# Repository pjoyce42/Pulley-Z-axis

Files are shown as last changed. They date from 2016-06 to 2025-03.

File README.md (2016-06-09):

# Pulley-Z-axis
a metal core xy printer with pulleys for the z-axis

This is an open source, 3D printer with a sheet metal frame. The intent of this design is to provide a robust mechanical design that is easy for any machine shop to manufacture. Currently, the design does require use of a breakpress and laser cutter, but all the bends are sharp 90deg, and the parts could be modified to use off the shelf (or printed) corner brackets. All individual printed parts are relatively small, and there is minimal support required. I tried to reuse parts as much as possible to reduce the unique part count.

In addition to the sheet metal frame, I have designed a hotend mount with an integrated strain gauge. My hope is that the strain gauge can be used for experimentation to provide an objective measurement that can be used to troubleshoot errors, optimize print settings, and help gain better insight into the physics of the printing process. I also hope to use the strian gauge in the auto bed leveling process in place of an induction sensor, or limit switches. 

Here is a partial to-do list:

	• Bowden tube ingress location
	• Spool holder
	• Door
	• Carrying Handles
	• Power plug mount
	• e-stop switch
	• Webcam mount
		○ LED strip mount
	• Validate Bed design
	• Switches for vaious electronics parts
		○ Rpi
		○ Main power
		○ Relays
			§ Hot end fan
			§ PrintrBoard
			§ LEDs
			§ Heated bed
	• Design strain gauge logging interface
	• Write software to emulate z-switch based on strain gauge reading
	
	If you have any interest in helping, or questions about the design please reach out through github.

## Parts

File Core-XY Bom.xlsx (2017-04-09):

ITEM NO. | PART NUMBER | QTY .
30 | _608 | 1
52 | 30x30 fan | 3
62 | 8x3mm magnet | 4
61 | 9541K1 | 4
31 | BEARING INSERT | 1
44 | Bed bearing mount | 2
66 | Connector^Endstop_Op to_TCST2103 | 5
13 | core-XY bed | 1
22 | e3d .40mm nozzle | 1
21 | e3dv6 heater block | 1
20 | e3dv6 heatsink | 1
4 | Enclosure back | 1
3 | Enclosure front | 1
47 | Enclosure side panel | 2
5 | Enclosure top | 1
38 | end stop trigger | 1
48 | end stop trigger | 2
50 | end stop trigger | 2
33 | extruder arm | 1
29 | Extruder base | 1
25 | filament | 1
40 | filament spool holder | 1
42 | gantry holder | 2
49 | gantry holder-bushing | 2
39 | hatchbox filament spool | 1
12 | heated bed spacer | 1
24 | heater core | 1
32 | HOBBED PULLEY | 1
26 | hotend clamp and fan mount | 1
9 | hotend mount | 1
37 | hotend mount-bushing | 1
11 | Hotend strain gauge mount | 1
46 | lift notch | 2
67 | linear bearing | 6
43 | linear rod | 2
53 | linear rod | 4
10 | loadcell | 1
58 | M2X10 | 4
63 | M3x20 | 4
35 | M3x35 | 1
51 | M4 V-groove pulley | 20
41 | M4X25 | 16
8 | mk2b heated bed | 1
14 | motion nut | 1
65 | PCB^Endstop_Opto_TCS T2103 | 5
27 | print cooling nozzle | 1
28 | print cooling nozzle mirror | 1
15 | printrboard | 1
16 | printrboard mount | 1
17 | psu | 1
45 | PULLEY SPACER 1 | 2
59 | PULLEY SPACER 1 | 4
60 | PULLEY SPACER 1 | 4
68 | PULLEY SPACER 1 | 6
19 | raspberrypi_b_+_(assem bly) | 1
18 | rpi board mount | 1
36 | sheet metal gantry | 1
34 | SPRING | 1
23 | steel heat break | 1
54 | STEPPER | 4
64 | TCST2103^Endstop_Opto _TCST2103 | 5
6 | threaded rod | 1
55 | TUNING PEG | 4
57 | tuning peg mount | 4
56 | TUNING PEG RETAINER | 4
2 | XYbase | 1
1 | XY-frame | 1
7 | z-coupler | 1

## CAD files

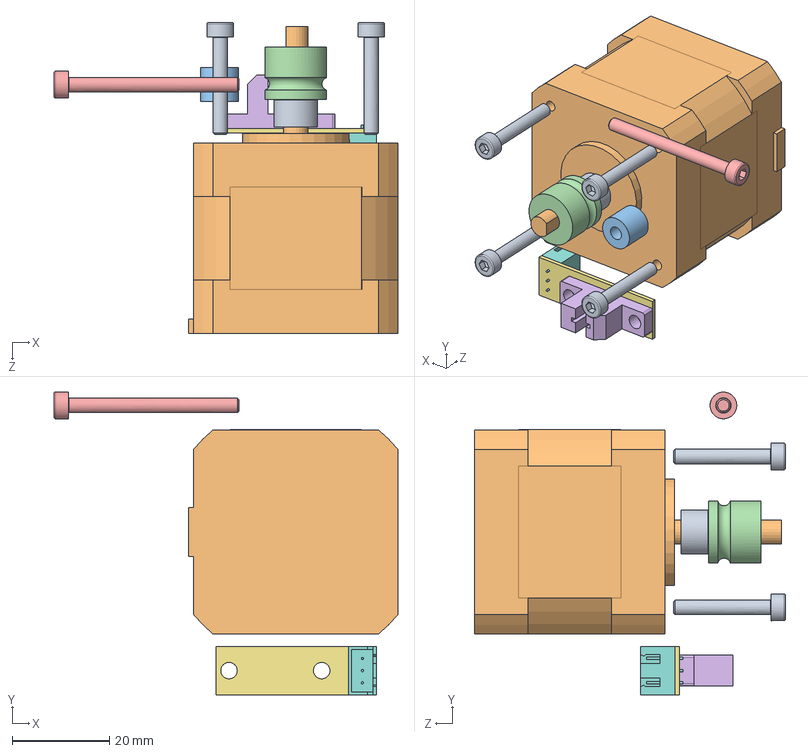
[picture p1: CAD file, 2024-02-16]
Extruder/Extruder.SLDASM
70.7 x 62.2 x 63.9 mm
M3x20 x 4
BEARING INSERT
M3x35
TCST2103^Endstop_Opto_TCST2103
PCB^Endstop_Opto_TCST2103
Connector^Endstop_Opto_TCST2103
MK8 HOBBED GEAR

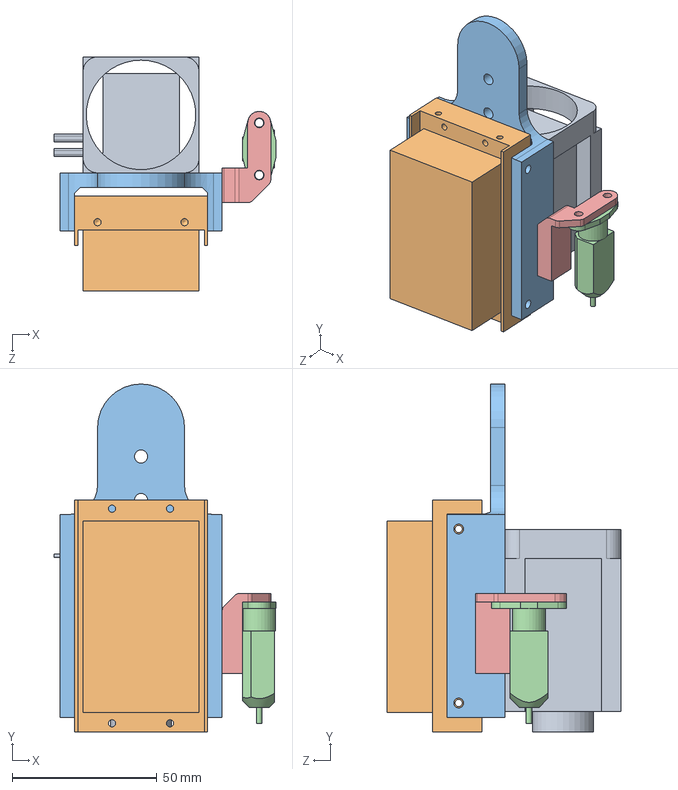
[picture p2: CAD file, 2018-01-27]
Laser/Laser Mount.SLDASM
76.5 x 120.0 x 80.8 mm
Laser Diode
Laser Driver
Laser Mount
BLTouch Smart
BLTouch mount

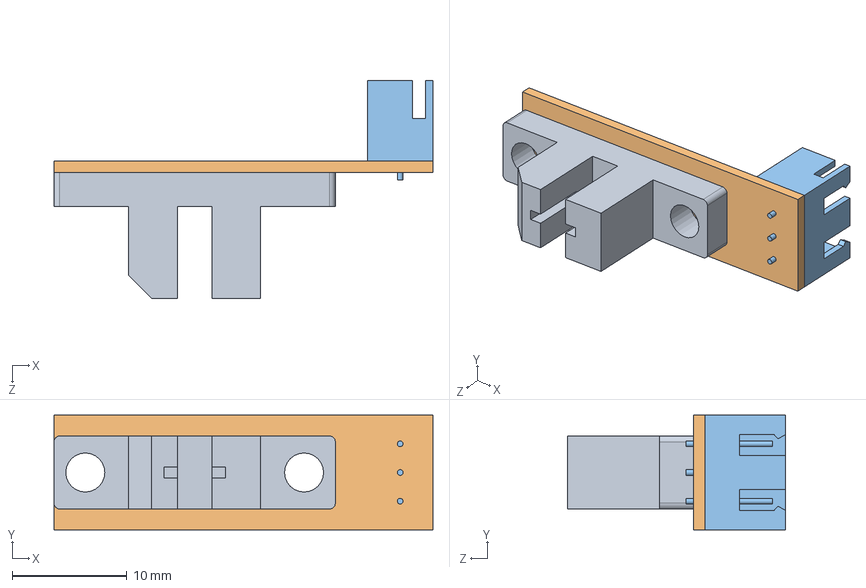
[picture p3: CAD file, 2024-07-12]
BortBot - Nov 2023/Endstop_Opto_TCST2103 - Nov 2023.SLDASM
33.0 x 10.0 x 19.0 mm
TCST2103^Endstop_Opto_TCST2103 - Nov 2023
PCB^Endstop_Opto_TCST2103 - Nov 2023
Connector^Endstop_Opto_TCST2103 - Nov 2023

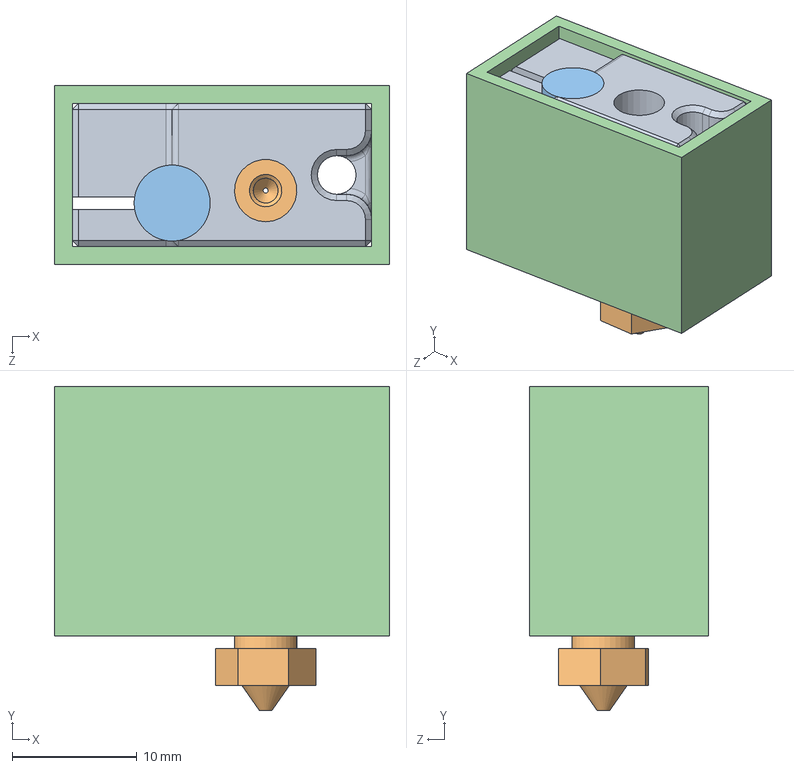
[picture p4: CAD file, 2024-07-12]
BortBot - Nov 2023/e3dv6 standin - Nov 2023.SLDASM
26.9 x 26.0 x 14.4 mm
E3d Volcano block - Nov 2023
e3d .40mm nozzle - Nov 2023
heater core - Nov 2023
Volcano Sock - Nov 2023

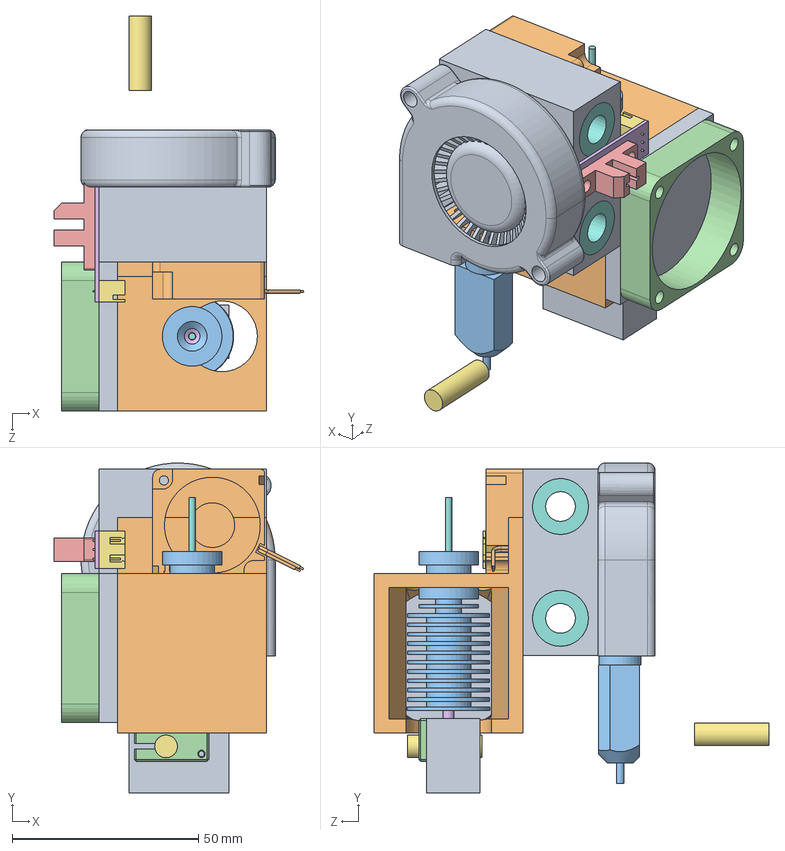
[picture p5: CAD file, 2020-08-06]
Modular Hot End/Modular Hot End.SLDASM
66.9 x 88.5 x 105.9 mm
Modular Hot End
Hot End Module
e3dv6 heatsink
e3dv6 heater block
e3d .40mm nozzle
steel heat break
heater core x 2
filament
BLTouch Angle Bracket
BLTouch Smart
40mmx40mm fan
TCST2103^Endstop_Opto_TCST2103
PCB^Endstop_Opto_TCST2103
Connector^Endstop_Opto_TCST2103
linear bearing x 2
Radial blower 30x10 v2

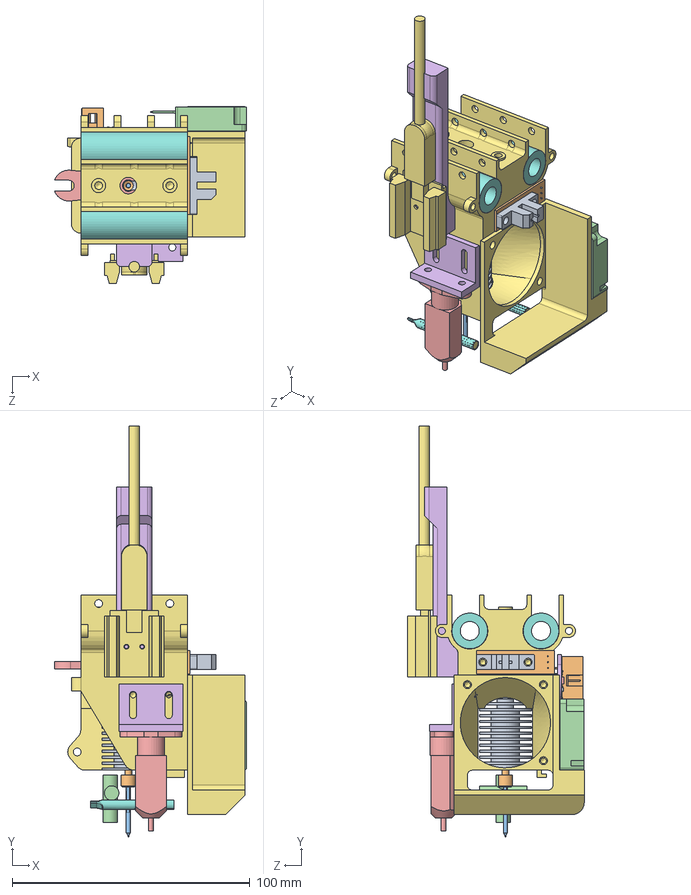
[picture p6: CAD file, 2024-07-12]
BortBot - Nov 2023/Bort Hot End Assy - Nov 2023.SLDASM
80.9 x 173.0 x 74.3 mm
e3dv6 heatsink - Nov 2023 x 2
steel heat break - Nov 2023 x 2
filament - Nov 2023 x 2
heater core - Nov 2023 x 2
BLTouch Smart - Nov 2023
BLTouch Angle Bracket - Nov 2023
Bort Hot End - Nov 2023
linear bearing - Nov 2023 x 2
TCST2103^Endstop_Opto_TCST2103 - Nov 2023
PCB^Endstop_Opto_TCST2103 - Nov 2023
Connector^Endstop_Opto_TCST2103 - Nov 2023
Radial blower 30x10 v2 - Nov 2023
collect clip - Nov 2023
Mini HDMI breakout board mount - Nov 2023
Micro HDMI Breakout board - Nov 2023
SOLID.step x 3
SOLID001.step
SOLID002.step
SOLID003.step x 6
SOLID005.step
SOLID010.step
Duet3_accelerometer PCB.step
Fan duct 3 + accel - Nov 2023
cooling tusk - Nov 2023 x 2

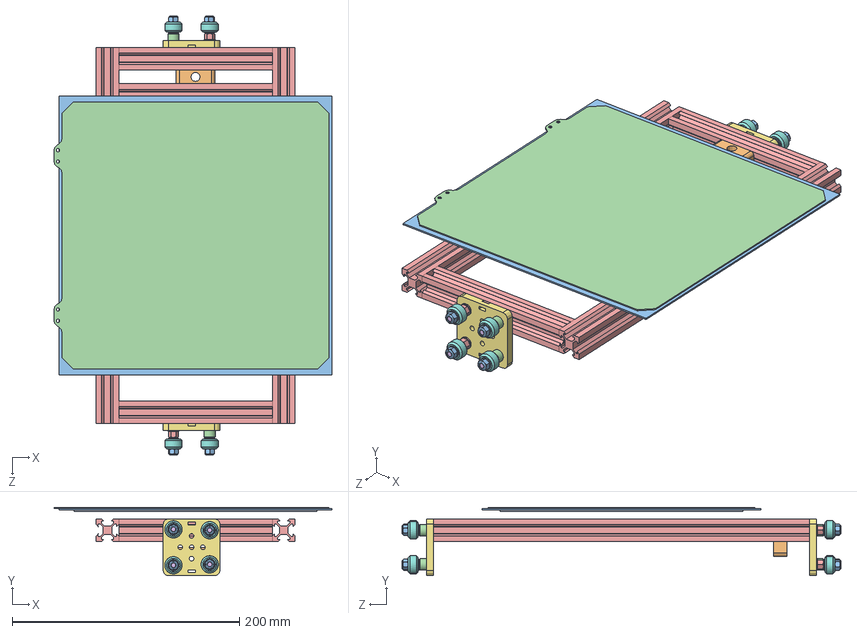
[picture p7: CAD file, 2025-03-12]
V-bed 3.SLDASM
244.5 x 60.2 x 385.8 mm
mk2b heated bed
8mm Acme Anti Backlash Nut Block
Heated Bed Platen
235 x 235 PEI build Plate
t-slot generic x 4
Low Profile Screw M5 x 8
Mini V Wheel Plate x 2
Delrin Mini V Wheel x 8
Ball Bearing 5 x 10 x 4.2 x 16
Precision Shim 8 x 5 x 1 x 16
Nylon Insert Lock Nut M5 x 8
Aluminum Spacer 6mm x 4
Mini Eccentric Spacer 6mm x 4

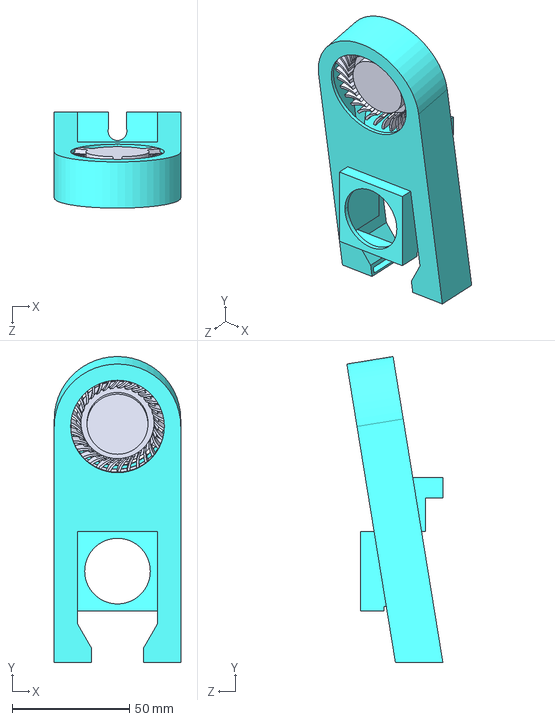
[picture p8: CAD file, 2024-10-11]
Simulations/Bort Hot End, Assy, Vertical Rails.STEP
54.0 x 130.6 x 41.1 mm
Blower fan 50mm
Fan shroud, Bortbot, vert

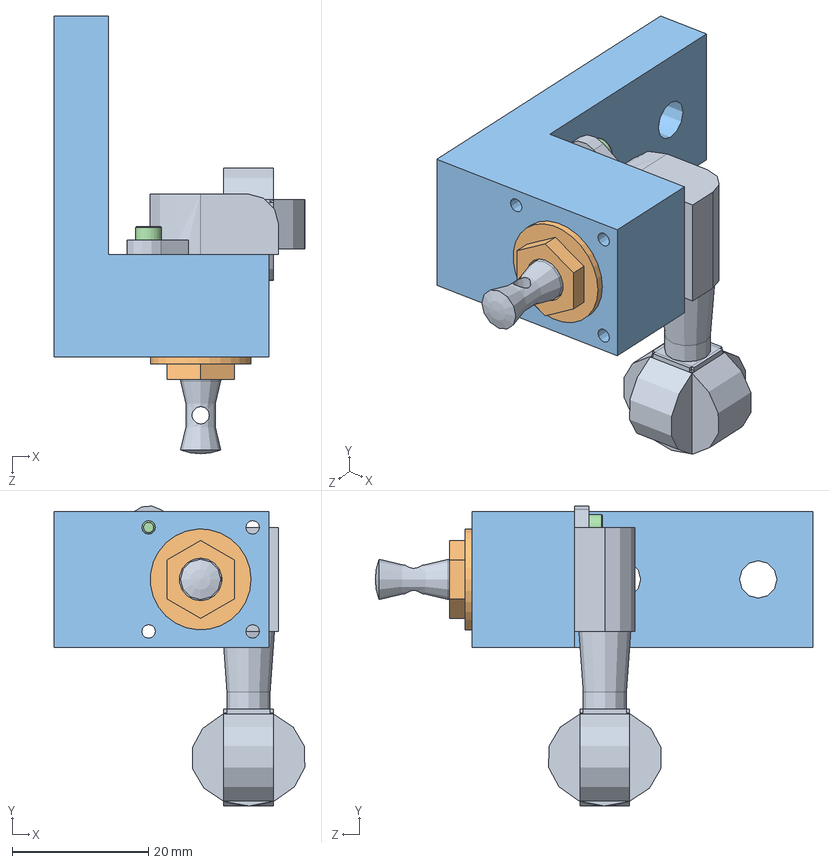
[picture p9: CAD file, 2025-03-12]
tuning peg tensioner 2.SLDASM
36.8 x 44.0 x 64.2 mm
TUNING PEG
TUNING PEG RETAINER
tuning peg mount 2
M2X10

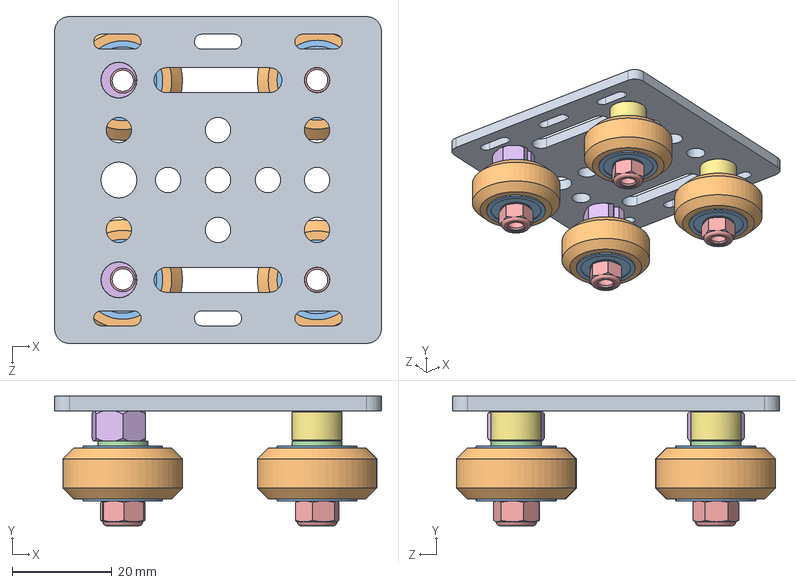
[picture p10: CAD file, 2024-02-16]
BortBot - Nov 2023/V-Slot Gantry Plate 1 - Nov 2023.SLDASM
65.5 x 26.0 x 65.5 mm
V-Slot Gantry Plate 20mm
Solid V Wheel x 4
Ball Bearing 5 x 16 x 5 x 8
Precision Shim 10 x 5 x 1 x 8
Nylon Insert Lock Nut M5 x 4
Eccentric Spacer 6mm x 2
Aluminum Spacer 6mm x 2

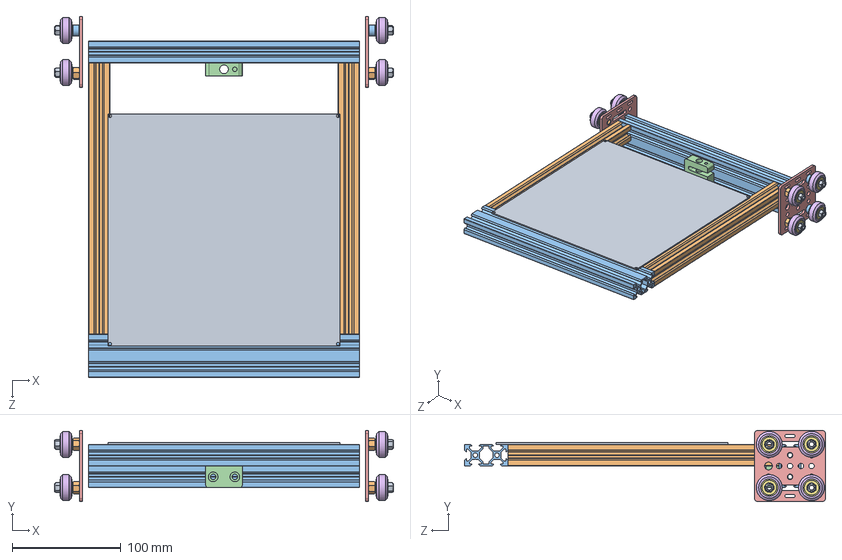
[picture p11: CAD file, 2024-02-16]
BortBot - Nov 2023/V-bed - Nov 2023.SLDASM
312.4 x 65.5 x 332.8 mm
mk2b heated bed
V-Slot 20x20x250 Linear Rail x 2
V-Slot 20x40x250 Linear Rail x 2
8mm Acme Anti Backlash Nut Block
V-Slot Gantry Plate 20mm x 2
Solid V Wheel x 8
Ball Bearing 5 x 16 x 5 x 16
Precision Shim 10 x 5 x 1 x 16
Nylon Insert Lock Nut M5 x 8
Eccentric Spacer 6mm x 4
Aluminum Spacer 6mm x 4

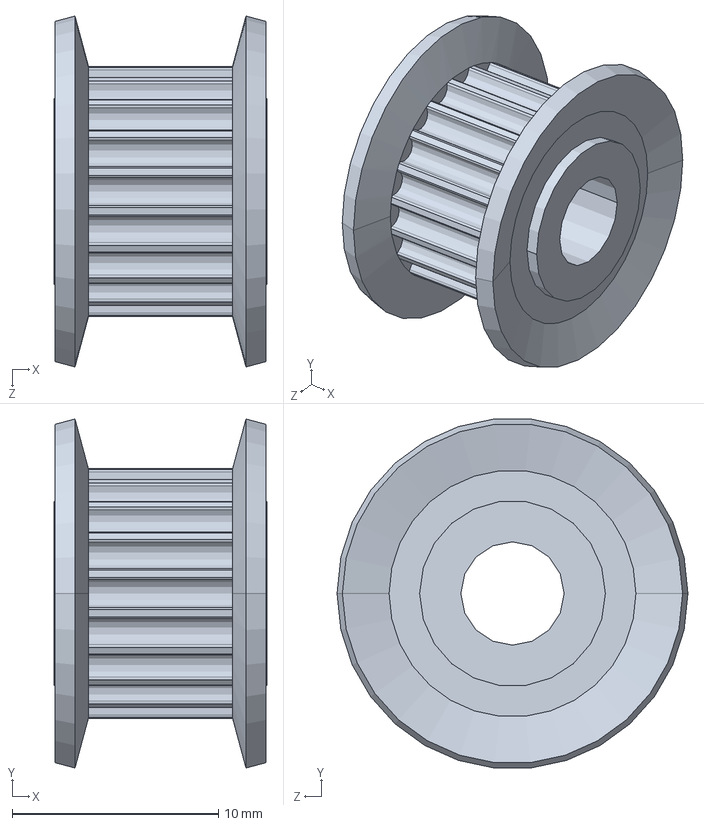
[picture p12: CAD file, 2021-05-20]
DWG Modular/GPA20GT2060_A_H5.sldasm
10.3 x 16.9 x 17.0 mm

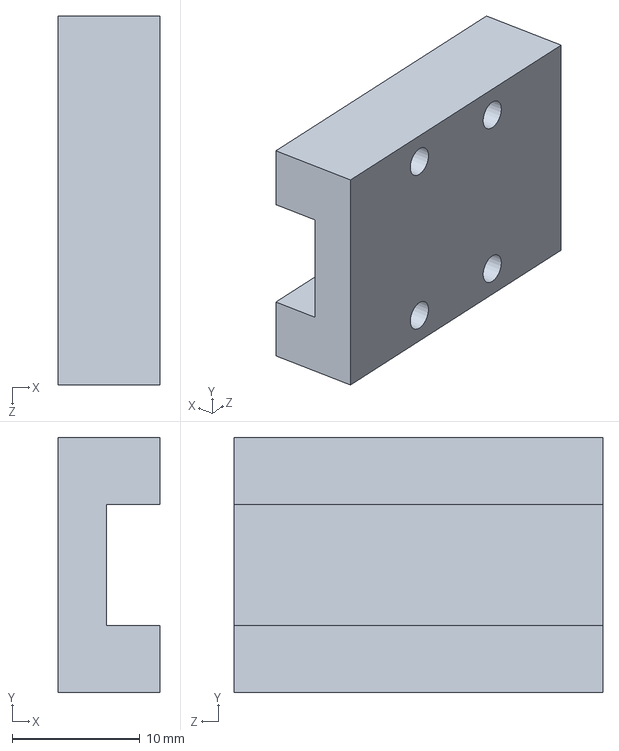
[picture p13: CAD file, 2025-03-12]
MGN9C Rail assy.SLDPRT
8.00 x 20.0 x 28.9 mm

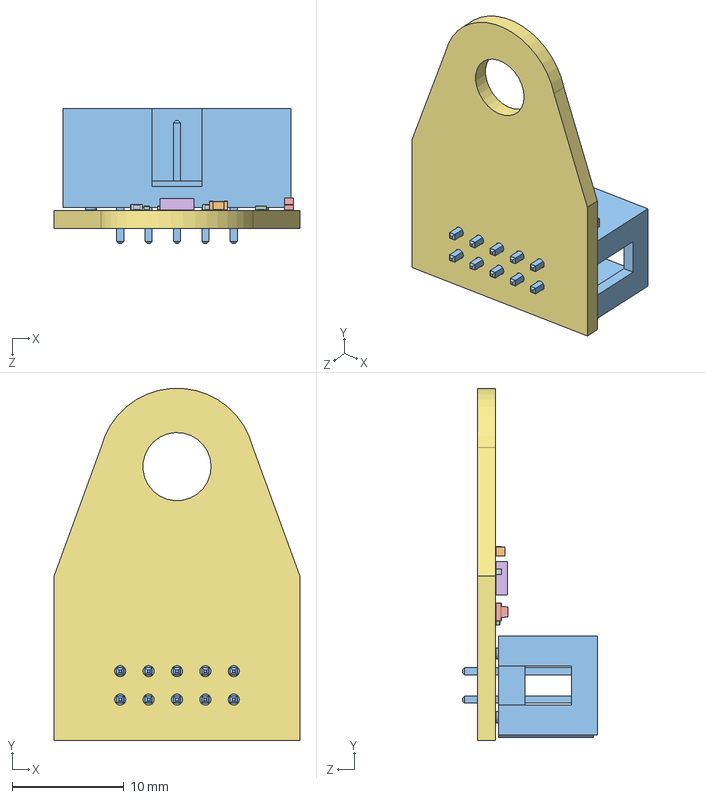
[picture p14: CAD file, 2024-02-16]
BortBot - Nov 2023/Duet3_accelerometer - Nov 2023.SLDASM
22.0 x 31.5 x 12.1 mm
SOLID.step x 3
SOLID001.step
SOLID002.step
SOLID003.step x 6
SOLID005.step
SOLID010.step
Duet3_accelerometer PCB.step

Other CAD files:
BortBot - Nov 2023/Solid V Wheel - Nov 2023.SLDASM
XY Gantry, Linear Rails, Assy.SLDASM
BortBot - Nov 2023/M4 PULLEY ASSEMBLY - Nov 2023.sldasm
Omron_Mag_Probe_Assembly.STEP.SLDASM
12 x 4 x 4 bearing.SLDPRT
235 x 235 PEI build Plate.SLDPRT
25x25x10 evercool fan.SLDPRT
2mm dowel.SLDPRT
30x30 fan.SLDPRT
3D_PCB4_2025-02-06 -2.SLDASM
3D_PCB4_2025-02-06.SLDASM
3D_PCB4_2025-02-06.step
40mm fan duct mirror.SLDPRT
40mmx40mm fan.SLDPRT
4mm dowel.SLDPRT
4mm linear bearing.SLDPRT
5010 fan mount.SLDPRT
604ZZ Bearing.SLDPRT
625vv.sldprt
6x3_Magnet.STEP.SLDPRT
9541K100_BUMPER WITH THREADED STUD.SLDPRT
A30 - Connector.SLDPRT
ASUS Blower fan.SLDPRT
BLTouch Spacer.SLDPRT
BLTouch sheet metal mount.SLDDRW
BLTouch sheet metal mount.SLDPRT
Bed Probe.SLDPRT
Bed bearing and nut.SLDASM
Bed bearing mount.SLDPRT
Belt1.SLDPRT
Blower fan 50mm.SLDPRT
Bort Hot End - 90deg rotate.SLDPRT
Bort Hot End - Mod.SLDPRT
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

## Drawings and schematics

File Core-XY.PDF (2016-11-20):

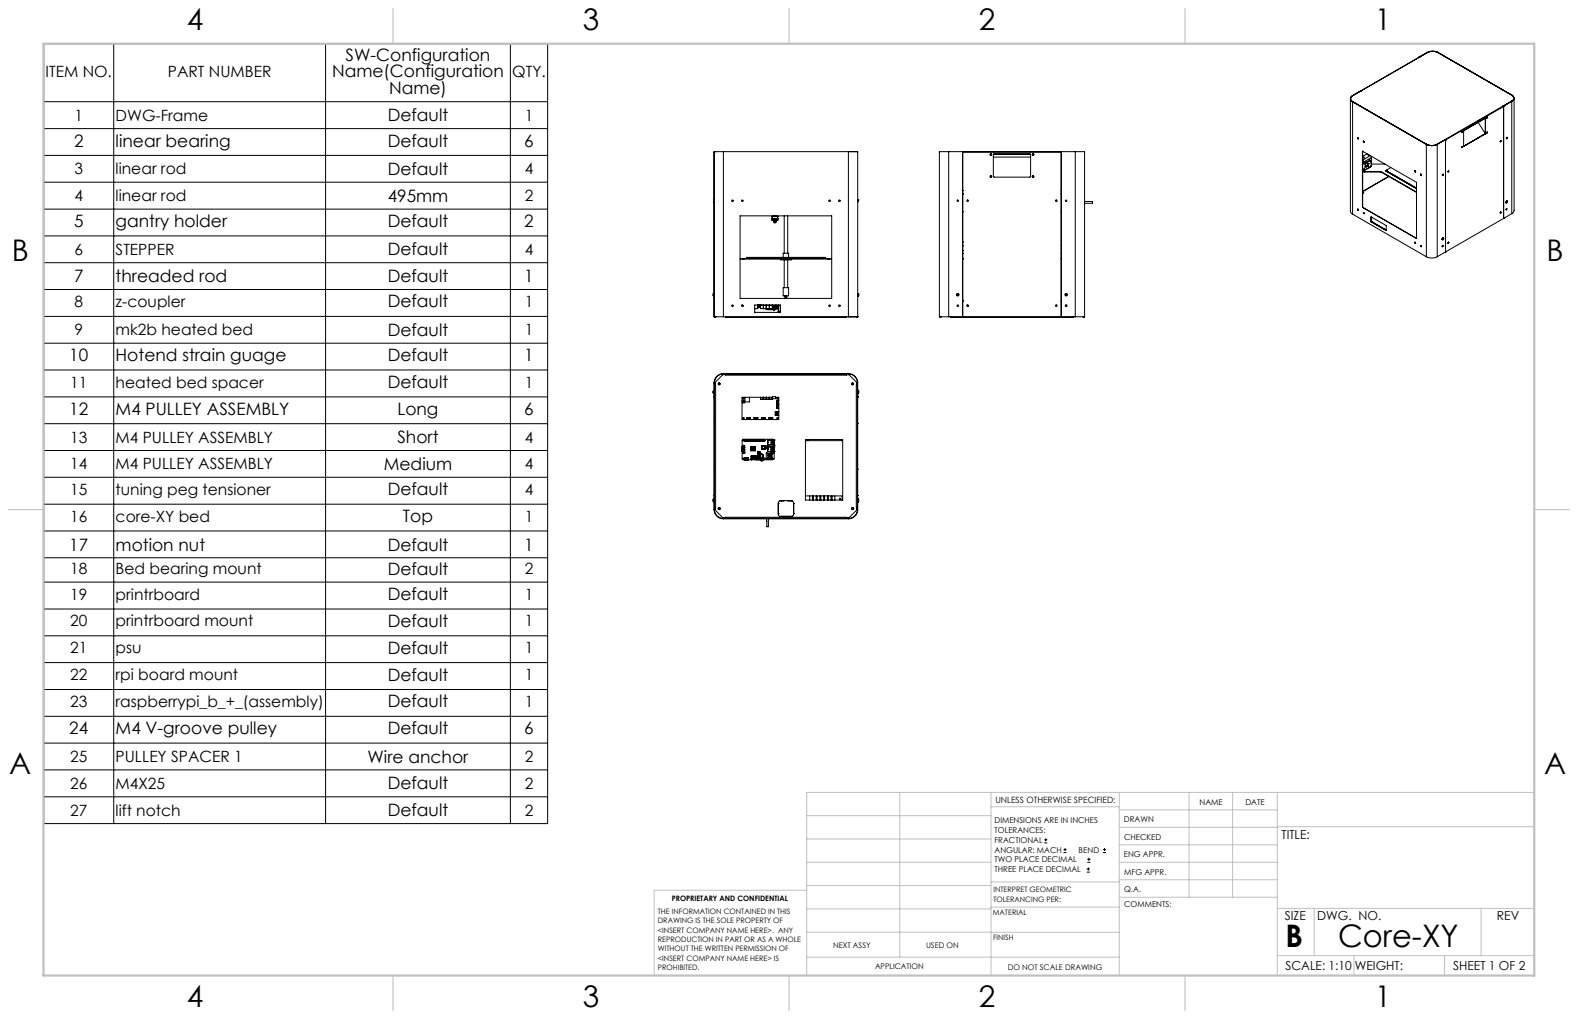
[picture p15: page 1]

ITEM NO. | PART NUMBER | SW-Configuration Name(Configuration Name) | QTY.

1 | DWG-Frame | Default | 1
2 | linear bearing | Default | 6
3 | linear rod | Default | 4
4 | linear rod | 495mm | 2
5 | gantry holder | Default | 2
6 | STEPPER | Default | 4
7 | threaded rod | Default | 1
8 | z-coupler | Default | 1
9 | mk2b heated bed | Default | 1
10 | Hotend strain guage | Default | 1
11 | heated bed spacer | Default | 1
12 | M4 PULLEY ASSEMBLY | Long | 6
13 | M4 PULLEY ASSEMBLY | Short | 4
14 | M4 PULLEY ASSEMBLY | Medium | 4
15 | tuning peg tensioner | Default | 4
16 | core-XY bed | Top | 1
17 | motion nut | Default | 1
18 | Bed bearing mount | Default | 2
19 | printrboard | Default | 1
20 | printrboard mount | Default | 1
21 | psu | Default | 1
22 | rpi board mount | Default | 1
23 | raspberrypi_b_+_(assembly) | Default | 1
24 | M4 V-groove pulley | Default | 6
25 | PULLEY SPACER 1 | Wire anchor | 2
26 | M4X25 | Default | 2
27 | lift notch | Default | 2

UNLESS OTHERWISE SPECIFIED: | | NAME | DATE
DIMENSIONS ARE IN INCHES TOLERANCES: FRACTIONAL ANGULAR: MACH BEND TWO PLACE DECIMAL THREE PLACE DECIMAL | DRAWN

CHECKED | | | TITLE:

ENG APPR.
MFG APPR.

INTERPRET GEOMETRIC TOLERANCING PER: | Q.A.
MATERIAL | | SIZE B | DWG. NO. Core-XY | REV

PROPRIETARY AND CONFIDENTIAL
THE INFORMATION CONTAINED IN THIS
DRAWING IS THE SOLE PROPERTY OF
<INSERT COMPANY NAME HERE>. ANY
REPRODUCTION IN PART OR AS A WHOLE
WITHOUT THE WRITTEN PERMISSION OF
<INSERT COMPANY NAME HERE> IS
PROHIBITED.

NEXT ASSY | USED ON | FINISH

APPLICATION | DO NOT SCALE DRAWING | | SCALE: 1:10 WEIGHT: | | SHEET 1 OF 2

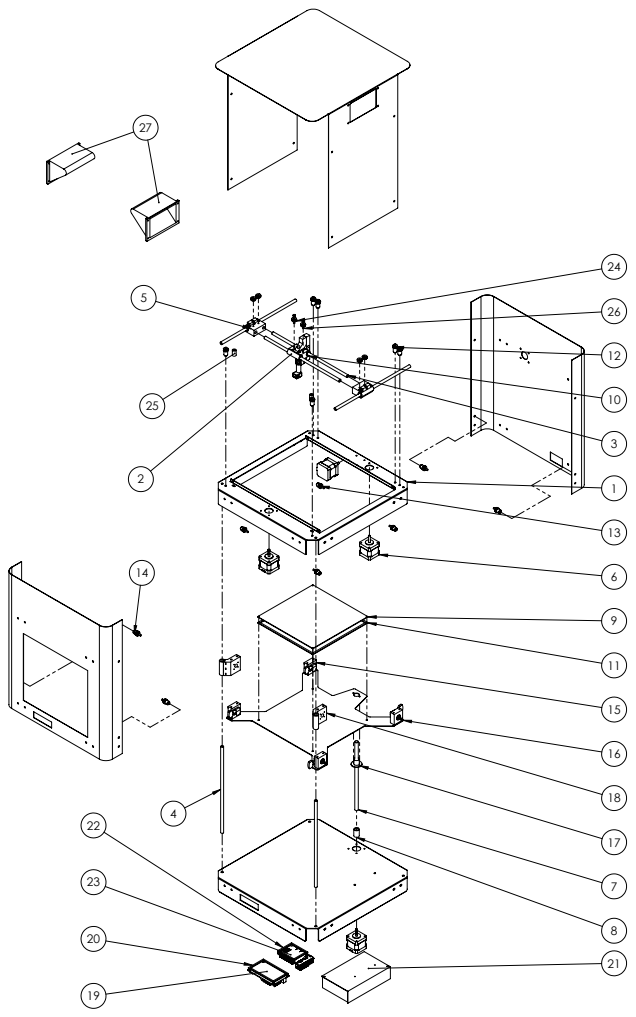
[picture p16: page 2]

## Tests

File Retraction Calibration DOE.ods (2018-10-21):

Run | X1 | X2 | X3 | X4 | X5 | X6 | X7 | Y1 | Y2
3 | -1 | 1 | -1 | -1 | 1 | -1 | 1 | 1 | 1
1 | -1 | -1 | -1 | 1 | 1 | 1 | -1 | 7 | 2
7 | -1 | 1 | 1 | -1 | -1 | 1 | -1 | 2 | 3
5 | -1 | -1 | 1 | 1 | -1 | -1 | 1 | 5 | 4
6 | 1 | -1 | 1 | -1 | 1 | -1 | -1 | 6 | 5
8 | 1 | 1 | 1 | 1 | 1 | 1 | 1 | 3 | 6
4 | 1 | 1 | -1 | 1 | -1 | -1 | -1 | 4 | 7
2 | 1 | -1 | -1 | -1 | -1 | 1 | 1 | 8 | 8
IDEAL | -1 | 1 | 0 | 0 | 1 | 0 | 0
 | Extra Restart Dist | Retract Dist | Layer Ht | Coast Dist | Wipe Dist | Retract During | Cooling Fan
1 | 0mm | 1.2mm | 0.15mm | 2mm | 2mm | Yes | 40.00%
2 | -1mm | 1.2mm | 0.15mm | 1.4mm | 1mm | Yes | 100.00%
3 | 0mm | 4mm | 0.15mm | 1.4mm | 2mm | No | 100.00%
4 | -1mm | 4mm | 0.15mm | 2mm | 1mm | No | 40.00%
5 | 0mm | 1.2mm | 0.4mm | 2mm | 1mm | No | 100.00%
6 | -1mm | 1.2mm | 0.4mm | 1.4mm | 2mm | No | 40.00%
7 | 0mm | 4mm | 0.4mm | 1.4mm | 1mm | Yes | 40.00%
8 | -1mm | 4mm | 0.4mm | 2mm | 2mm | Yes | 100.00%
IDEAL | 0mm | 4mm | 0.15mm | 1.4mm | 2mm | Yes | 40

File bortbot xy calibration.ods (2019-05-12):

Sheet: Sheet1
Trial run | X nominal | Y nominal | X1 real | Y1 Real | X2 real | Y2 Real | Xavg real | Yavg Real | X steps/mm | Y Steps/mm | X % error | Y % error
0 | 100 | 100 | 101.06 | 97.1 | 101.55 | 96.88 | 101.305 | 96.99 | 272.54 | 134.12 | 1.30500000000001 | -3.01000000000001
1 | 100 | 100 | 102.17 | 94.16 | 103.29 | 94 | 102.73 | 94.08 | 276.096647 | 130.082988 | 2.73 | -5.92
2 | 100 | 100 | 99.4 | 100.4 | 101.04 | 100.22 | 100.22 | 100.31 | 268.759512313832 | 138.268482142857 | 0.219999999999999 | 0.310000000000002
3 | 100 | 100 | 99.65 | 100.55 | 99.52 | 100.45 | 99.585 | 100.5 | 268.169539327312 | 137.841174501901 | -0.414999999999992 | 0.5
4 | 100 | 100 |  |  |  |  | #DIV/0! | #DIV/0! | 269.287080712268 | 137.15539751433 | #DIV/0! | #DIV/0!
5 | 100 | 100 |  |  |  |  | #DIV/0! | #DIV/0! | #DIV/0! | #DIV/0! | #DIV/0! | #DIV/0!
6 | 100 | 100 |  |  |  |  | #DIV/0! | #DIV/0! | #DIV/0! | #DIV/0! | #DIV/0! | #DIV/0!
7 | 100 | 100 |  |  |  |  | #DIV/0! | #DIV/0! | #DIV/0! | #DIV/0! | #DIV/0! | #DIV/0!
8 | 100 | 100 |  |  |  |  | #DIV/0! | #DIV/0! | #DIV/0! | #DIV/0! | #DIV/0! | #DIV/0!
9 | 100 | 100 |  |  |  |  | #DIV/0! | #DIV/0! | #DIV/0! | #DIV/0! | #DIV/0! | #DIV/0!
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

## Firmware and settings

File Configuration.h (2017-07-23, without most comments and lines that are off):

#define CONFIGURATION_H
#define CONFIGURATION_H_VERSION 010100
#define STRING_CONFIG_H_AUTHOR "(Patrick Joyce)" // Who made the changes.
#define SHOW_BOOTSCREEN
#define STRING_SPLASH_LINE1 SHORT_BUILD_VERSION // will be shown during bootup in line 1
#define STRING_SPLASH_LINE2 WEBSITE_URL         // will be shown during bootup in line 2
#define SERIAL_PORT 0
#define BAUDRATE 250000
  #define MOTHERBOARD BOARD_PRINTRBOARD
#define CUSTOM_MACHINE_NAME "BORT1"
#define EXTRUDERS 1
#define POWER_SUPPLY 0
#define TEMP_SENSOR_0 -1 //legacy from QU-BD Ups
#define TEMP_SENSOR_1 0
#define TEMP_SENSOR_2 0
#define TEMP_SENSOR_3 0
#define TEMP_SENSOR_4 0
#define TEMP_SENSOR_BED 0
#define DUMMY_THERMISTOR_998_VALUE 25
#define DUMMY_THERMISTOR_999_VALUE 100
#define MAX_REDUNDANT_TEMP_SENSOR_DIFF 10
#define TEMP_RESIDENCY_TIME 10  // (seconds)
#define TEMP_HYSTERESIS 3       // (degC) range of +/- temperatures considered "close" to the target one
#define TEMP_WINDOW     1       // (degC) Window around target to start the residency timer x degC early.
#define TEMP_BED_RESIDENCY_TIME 10  // (seconds)
#define TEMP_BED_HYSTERESIS 3       // (degC) range of +/- temperatures considered "close" to the target one
#define TEMP_BED_WINDOW     1       // (degC) Window around target to start the residency timer x degC early.
#define HEATER_0_MINTEMP 5
#define HEATER_1_MINTEMP 5
#define HEATER_2_MINTEMP 5
#define HEATER_3_MINTEMP 5
#define HEATER_4_MINTEMP 5
#define BED_MINTEMP 5
#define HEATER_0_MAXTEMP 275
#define HEATER_1_MAXTEMP 275
#define HEATER_2_MAXTEMP 275
#define HEATER_3_MAXTEMP 275
#define HEATER_4_MAXTEMP 275
#define BED_MAXTEMP 150
#define PIDTEMP
#define BANG_MAX 255 // limits current to nozzle while in bang-bang mode; 255=full current
#define PID_MAX BANG_MAX // limits current to nozzle while PID is active (see PID_FUNCTIONAL_RANGE below); 255=full current
  #define PID_FUNCTIONAL_RANGE 10 // If the temperature difference between the target temperature and the actual temperature
  #define K1 0.95 //smoothing factor within the PID
  #define  DEFAULT_Kp 32.25
  #define  DEFAULT_Ki 3.67
  #define  DEFAULT_Kd 70.8
#define MAX_BED_POWER 255 // limits duty cycle to bed; 255=full current
#define PREVENT_COLD_EXTRUSION
#define EXTRUDE_MINTEMP 170
#define PREVENT_LENGTHY_EXTRUDE
#define EXTRUDE_MAXLENGTH 200
#define THERMAL_PROTECTION_HOTENDS // Enable thermal protection for all extruders
#define THERMAL_PROTECTION_BED     // Enable thermal protection for the heated bed
#define USE_XMIN_PLUG
#define USE_YMIN_PLUG
#define USE_ZMIN_PLUG
#define ENDSTOPPULLUPS // Comment this out (using // at the start of the line) to disable the endstop pullup resistors
#define X_MIN_ENDSTOP_INVERTING false // set to true to invert the logic of the endstop.
#define Y_MIN_ENDSTOP_INVERTING false // set to true to invert the logic of the endstop.
#define Z_MIN_ENDSTOP_INVERTING false // set to true to invert the logic of the endstop.
#define X_MAX_ENDSTOP_INVERTING false // set to true to invert the logic of the endstop.
#define Y_MAX_ENDSTOP_INVERTING false // set to true to invert the logic of the endstop.
#define Z_MAX_ENDSTOP_INVERTING false // set to true to invert the logic of the endstop.
#define Z_MIN_PROBE_ENDSTOP_INVERTING false // set to true to invert the logic of the probe.
#define DEFAULT_AXIS_STEPS_PER_UNIT   { 80, 80, 4000, 500 }
#define DEFAULT_MAX_FEEDRATE          { 136.7, 67.06, 1511.81, 89.01 }
#define DEFAULT_MAX_ACCELERATION      { 5000, 5000, 100, 10000 }
#define DEFAULT_ACCELERATION          3000    // X, Y, Z and E acceleration for printing moves
#define DEFAULT_RETRACT_ACCELERATION  3000    // E acceleration for retracts
#define DEFAULT_TRAVEL_ACCELERATION   3000    // X, Y, Z acceleration for travel (non printing) moves
#define DEFAULT_XJERK                 20.0
#define DEFAULT_YJERK                 20.0
#define DEFAULT_ZJERK                  0.4
#define DEFAULT_EJERK                  5.0
#define X_PROBE_OFFSET_FROM_EXTRUDER 10  // X offset: -left  +right  [of the nozzle]
#define Y_PROBE_OFFSET_FROM_EXTRUDER 10  // Y offset: -front +behind [the nozzle]
#define Z_PROBE_OFFSET_FROM_EXTRUDER 0   // Z offset: -below +above  [the nozzle]
#define XY_PROBE_SPEED 8000
#define Z_PROBE_SPEED_FAST HOMING_FEEDRATE_Z
#define Z_PROBE_SPEED_SLOW (Z_PROBE_SPEED_FAST / 2)
#define Z_CLEARANCE_DEPLOY_PROBE   10 // Z Clearance for Deploy/Stow
#define Z_CLEARANCE_BETWEEN_PROBES  5 // Z Clearance between probe points
#define Z_PROBE_OFFSET_RANGE_MIN -20
#define Z_PROBE_OFFSET_RANGE_MAX 20
#define X_ENABLE_ON 0
#define Y_ENABLE_ON 0
#define Z_ENABLE_ON 0
#define E_ENABLE_ON 0 // For all extruders
#define DISABLE_X false
#define DISABLE_Y false
#define DISABLE_Z false
#define DISABLE_E false // For all extruders
#define DISABLE_INACTIVE_EXTRUDER true // Keep only the active extruder enabled.
#define INVERT_X_DIR false
#define INVERT_Y_DIR true
#define INVERT_Z_DIR false
#define INVERT_E0_DIR false
#define INVERT_E1_DIR false
#define INVERT_E2_DIR false
#define INVERT_E3_DIR false
#define INVERT_E4_DIR false
#define X_HOME_DIR -1
#define Y_HOME_DIR -1
#define Z_HOME_DIR -1
#define X_MIN_POS 0
#define Y_MIN_POS 0
#define Z_MIN_POS 0
#define X_MAX_POS 200
#define Y_MAX_POS 200
#define Z_MAX_POS 200
#define MIN_SOFTWARE_ENDSTOPS
#define MAX_SOFTWARE_ENDSTOPS
#define HOMING_FEEDRATE_XY (50*60)
#define HOMING_FEEDRATE_Z  (4*60)
#define EEPROM_SETTINGS // Enable for M500 and M501 commands
#define EEPROM_CHITCHAT   // Give feedback on EEPROM commands. Disable to save PROGMEM.
#define HOST_KEEPALIVE_FEATURE        // Disable this if your host doesn't like keepalive messages
#define DEFAULT_KEEPALIVE_INTERVAL 2  // Number of seconds between "busy" messages. Set with M113.
#define PREHEAT_1_TEMP_HOTEND 180
#define PREHEAT_1_TEMP_BED     70
#define PREHEAT_1_FAN_SPEED     0 // Value from 0 to 255
#define PREHEAT_2_TEMP_HOTEND 240
#define PREHEAT_2_TEMP_BED    110
#define PREHEAT_2_FAN_SPEED     0 // Value from 0 to 255
#define PRINTJOB_TIMER_AUTOSTART
#define PRINTCOUNTER
#define LCD_LANGUAGE en
#define DISPLAY_CHARSET_HD44780 JAPANESE
#define SOFT_PWM_SCALE 0
#define SERVO_DELAY 300
#define DEFAULT_NOMINAL_FILAMENT_DIA 3.00   // (mm) Diameter of the filament generally used (3.0 or 1.75mm), also used in the slicer. Used to validate sensor reading.

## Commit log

2016-06-09 Upload solidworks assembly
    This is the initial model upload. The sheet metal is 95% complete, the printed parts are 90%, the electronics layout is 80%, and I still need to design a door
    [625vv.sldprt, Bed bearing and nut.SLDASM, Bed bearing mount.SLDPRT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]
2016-10-16 updates
    added lifting handle, weight reduction on bed support plate
    [Core-XY.SLDASM, DWG-Frame.SLDASM, Enclosure top.SLDPRT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]
2016-10-23 more details
    adding small finishing details to start printing parts
    [Bed bearing mount.SLDPRT, Core-XY.SLDASM, DWG-Frame.SLDASM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]
2016-10-24 begin documentation
    made exploded view and assembly drawing
    [Core-XY.SLDASM, Core-XY.SLDDRW, M4 PULLEY ASSEMBLY.sldasm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]
2016-10-30 prep for mfg
    made stl files, and added gdt to some parts
    [Bed bearing mount.SLDPRT, Bed bearing mount.STL, Core-XY.SLDASM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]
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2016-11-06 Revert "minor dwg change"
    This reverts commit 5182210faf61d8f11bfa9f020a0fec0bc8e869d2.
    [Core-XY.SLDASM, Core-XY.SLDDRW]
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2016-11-06 preping the printer layout
    setting up the simplify3d factory files
    [Core-XY.SLDASM, Core-XY.SLDDRW, z-coupler.SLDPRT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]
2016-11-20 gcode for more parts
    [Core-XY.SLDASM, Core-XY.SLDDRW]
2016-11-27 SIMULATING the hot end mount
    [40mmx40mm fan.SLDPRT, Core-XY.SLDASM, E3Dv6.sldprt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]
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2017-01-07 Printed bushing version
    I have added a bunch of new parts that would allow the printer to
    function using formed sheet metal rails, and 3D printed bushings instead
    of linear ball bearings
    [Core-XY.SLDASM, DWG-Frame.SLDASM, Hotend strain guage.SLDASM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]
2017-02-10 Clean up model and modify top panel
    Began changing the top/side panel to be 3 parts for ease of storage, and
    transportation. It appears that the whole printer could be flat-packed
    inside its own enclosure panel. And I think the mechanical parts would
    be extremely easy to mass produce.
    [Core-XY.SLDASM, DWG-Frame.SLDASM, Enclosure side panel.SLDPRT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]
2017-02-11 prep for finalizing the hot end cooler
    [25x25x10 evercool fan.SLDPRT, 30x30 fan.SLDPRT, Core-XY.SLDASM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]
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2017-03-17 added endstops and cable management
    [DWG-Frame.SLDASM, Enclosure back.SLDDRW, Enclosure back.SLDPRT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]
2017-03-26 added print cooling ducts and extruder
    [8x3mm magnet.SLDPRT, BEARING INSERT.sldprt, Core-XY Bom.xlsx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]
2017-03-27 update drawing and extruder and added screws
    [Core-XY.SLDDRW, DWG-Frame.SLDASM, Enclosure back.SLDPRT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]
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2017-04-10 new gantry mount, fix hole sizes, fix pulley mount
    [Bed bearing mount.SLDPRT, Bed bearing mount.STL, DWG-Frame.SLDASM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]
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2017-04-15 added filament sensor and clean up assembly tree
    [608 bearing.SLDPRT, BEARING INSERT.sldprt, DWG-Frame.SLDASM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]
2017-05-05 Tweaks and update some dims for printing tolerance
    [40mm fan duct mirror.SLDPRT, 40mm fan duct mirror.STL, 40mm fan duct.SLDPRT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]
2017-05-09 Update Z-axis pulley config
    [DWG-Frame.SLDASM, Heated Bed.SLDASM, Hotend strain guage.SLDASM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]
2017-05-23 Start V2 of the heated bed plate
    [Bed bearing mount.SLDPRT, DWG-Frame.SLDASM, Heated Bed.SLDASM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]
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2017-06-20 Update Enclosure
    Merge side panels into front or rear. Modify top to be screwed into
    sides. Design intent is to be able to remove the front and have full
    access to work on printer.
    [DWG-Frame.SLDASM, Enclosure back.SLDPRT, Enclosure front one piece.SLDPRT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]
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2017-07-23 custom marlin config file
    [Configuration.h]
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2017-10-15 add supports
    added extruded al beams to make new arrangement of pulleys for rev1 bed
    [DWG-Frame.SLDASM, XY-frame v2.SLDPRT, aluminum c channel.SLDPRT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]
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2017-11-04 Laser adapter
    file reorg and added mounting plate for laser diode and laser driver
    [40mm fan duct mirror.STL, 40mm fan duct.STL, 625vv.sldprt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]
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2018-01-27 Add BLTouch sensor and mount
    [BLTouch Smart.SLDPRT, BLTouch mount.SLDPRT, BLTouch sheet metal mount.SLDDRW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]
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2018-03-14 shortened hot end mount for stiffness
    [Hotend strain gauge mount.SLDPRT, hotend mount shortened.SLDPRT]
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2018-03-18 fixed mounting holes
    [hotend mount shortened.SLDPRT, hotend mount shortened.STL, printed foot.STL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]
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2018-10-21 added z-rod bearing clamp
    [Extruder.SLDASM, MK8 HOBBED GEAR.SLDPRT, Retraction Calibration DOE.ods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]
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2019-01-20 finalized design of new z-bed
    [Core-XY-mod.SLDASM, Duet3D Maestro mount.SLDPRT, Duet3D Maestro mount.STL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]
2019-05-12 v-slot redesign
    [Bort Hot End Assy.SLDASM, Bort Hot End.SLDPRT, Bort Hot End.STL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]
2019-05-12 minor print quality stuff
    [bortbot xy calibration.ods]
2019-05-14 Making x and z-axis plates
    [X-axis plate.SLDPRT, Z-nut follower.SLDASM, Z-nut follower.SLDPRT]
2019-05-14 more progess on v-slot
    [Bort Hot End Assy.SLDASM, Bort Hot End.SLDPRT, M4 V-groove pulley.SLDPRT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]
2019-05-21 hot end mount cfd and updates
    [Bort Hot End Assy.SLDASM, Bort Hot End.SLDPRT, Endstop_Opto_TCST2103.SLDASM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]
2019-06-01 new hot end and pulleys
    [Bort Hot End Assy.SLDASM, Bort Hot End.SLDPRT, E3d Volcano block.SLDPRT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]
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2020-08-06 updated to match IRL
    The CoreXY-Mod assembly is now a very close mechanical match to the real machine as its been for the last year. Also, I exported that assembly as both STEP and IGS for use with other CAD packages
    [Bort Hot End Assy.SLDASM, Core-XY-mod.SLDASM, DWG-Frame.SLDASM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]
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2021-08-22 pen end effector
    added hobby servo to pen end effector
    [DWG plate layout.prt, Pen End Effector.prt, Pen End Effector.stl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]
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2024-07-12 clean up and upgrades
    claned up cad. made a new directory for as built hardware
    [12 x 4 x 4 bearing.SLDPRT, 235 x 235 PEI build Plate.SLDPRT, ASUS Blower fan.SLDPRT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]
2024-08-03 nearly all new hot end
    polymer bushings also
    [40mmx40mm fan.SLDPRT, Bort Hot End - Mod.SLDPRT, Bort Hot End 2.SLDPRT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]
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

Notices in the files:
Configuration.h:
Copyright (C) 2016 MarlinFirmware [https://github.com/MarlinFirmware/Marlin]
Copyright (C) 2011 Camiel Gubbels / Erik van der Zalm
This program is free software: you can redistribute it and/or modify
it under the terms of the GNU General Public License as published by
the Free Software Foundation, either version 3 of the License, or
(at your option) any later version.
